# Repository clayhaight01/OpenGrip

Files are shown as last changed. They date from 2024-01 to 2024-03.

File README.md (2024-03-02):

# OpenGrip

### a simple, low-cost, robotics gripper

<div>
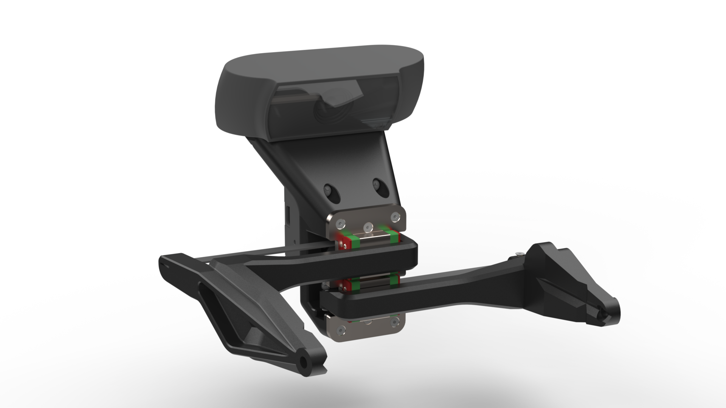
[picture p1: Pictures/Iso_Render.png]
Isometric Render of OpenGrip
  
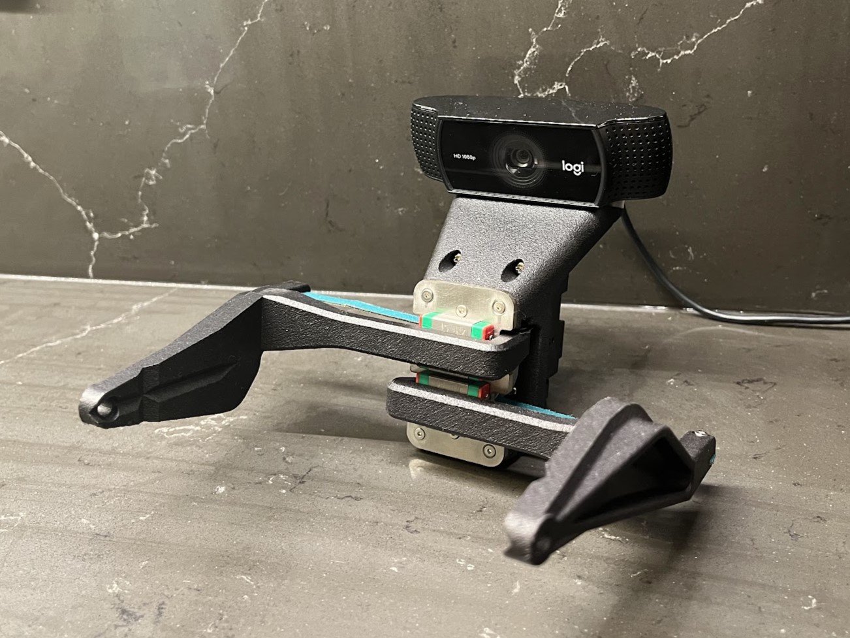
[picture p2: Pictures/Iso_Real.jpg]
Isometric View of the Actual OpenGrip
  
</div>

## overview

robotics grippers are often expensive, bulky, and challenging to integrate. OpenGrip offers a solution that is both affordable and user-friendly, without compromising on performance. 

### features

- **low cost**: by using only 5 custom parts and affordable hardware, OpenGrip significantly reduces costs, making it accessible for a wide range of users and applications

- **simple**: no belts, linkages, or gears - and constant force springs prevent collisions from damaging the gripper

- **high performance**: despite its cost-effectiveness, OpenGrip competes with the performance of grippers that are up to 50 times more expensive

- **adjustable compliance**: by using different winch materials (Nylon, Rubber, etc.) the compliance of the grasp can be adjusted

- **ease of use**: the Dynamixel servo motor makes OpenGrip extremely user-friendly. It can be controlled through ROS or any other Dynamixel-compatible control methods

## getting started

Assembly instructions can be found [here](https://docs.google.com/presentation/d/1iBIFQ8Uv3fJxjH3Wcjm2KIDGo_j1fCUzhZIH-ikzjmM/edit?usp=sharing)

BOM can be found [here](https://docs.google.com/spreadsheets/d/18ndGbQFCbwUeQNG1r3dqTShQs4zwCBGkiXpTbjC0DrM/edit?usp=sharing)

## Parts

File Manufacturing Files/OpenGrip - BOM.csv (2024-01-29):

OpenGrip | a simple, low cost, robotics gripper
Name | Configuration | Link | Price | Quantity | Total Price (USD) | Notes
Dynamixel Servo | XL430-W250 | https://www.robotis.us/dynamixel-xl430-w250-t/ | $49.90 | 1 | $49.90 | Use screws that come with it for pulley mounting
Constant Force Spring | 0.1x8x110 | https://www.aliexpress.com/item/1005002310168061.html | $6.52 | 2 | $13.04
Linear Rail & Carriage | 80 - MGN7C | https://www.aliexpress.com/item/1005004894759989.html | $13.41 | 2 | $26.82
Nylon Belt | 8in | https://www.mcmaster.com/6082K51-6082K202/ | $7.12 | 1 | $7.12 | If you want no compliance
Rubber Belt | 60mm | https://www.aliexpress.com/item/1005001961868127.html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 | $5.21 | 0 | $0.00 | If you want compliance
Silicone Padding | 300x30x1 | https://www.aliexpress.com/item/1005003757932880.html | $2.52 | 1 | $2.52
Heat Set Inserts | M2-M4 | https://www.aliexpress.com/item/1005005227477455.html | $18.93 | 1 | $18.93
M2 Flat Head | 5mm | https://www.mcmaster.com/92125A051/ | $10.80 | 1 | $10.80 | Multiple other sources
Screws | Cap | https://www.aliexpress.com/item/33033655207.html | $21.73 | 1 | $21.73
Screws | Flat | https://www.aliexpress.com/item/33033655207.html | $24.90 | 1 | $24.90
Webcam | C922X | https://www.amazon.com/Logitech-C922x-Pro-Stream-Webcam/dp/B01LXCDPPK | 79.99 | 0 | $0.00 | Optional
 |  |  |  | Total | $175.76
I used MJF for all the plastic parts from JLCPCB, but everything can be easily FDM printed.
File Name |  | Material | Manufacturing | Quantity | Notes
Gripper_Structure.STL |  | PA11/PLA | MJF/FDM | 1
Gripper_Jaw.STL |  | PA11/PLA | MJF/FDM | 2
CF_Spring_Idler.STL |  | PA11/PLA | MJF/FDM | 2
CF_Spring_Idler_Cap.STL |  | PA11/PLA | MJF/FDM | 2
Gripper_Carriage_Mount<...>.DXF or .STEP |  | Aluminum | Laser/Waterjet/CNC | 1 | I got from SendCutSend. If you want high force grasps, switch to stainless. If you want to lasercut/waterjet and countersink yourself, use the DXF. If you are CNCing use the STEP.
Gripper_Drive_Pulley.STL |  | PA11/PLA | MJF/FDM | 1
C922X_Pro_Clamp.STL |  | PA11/PLA | MJF/FDM | 0 | Optional, for webcam

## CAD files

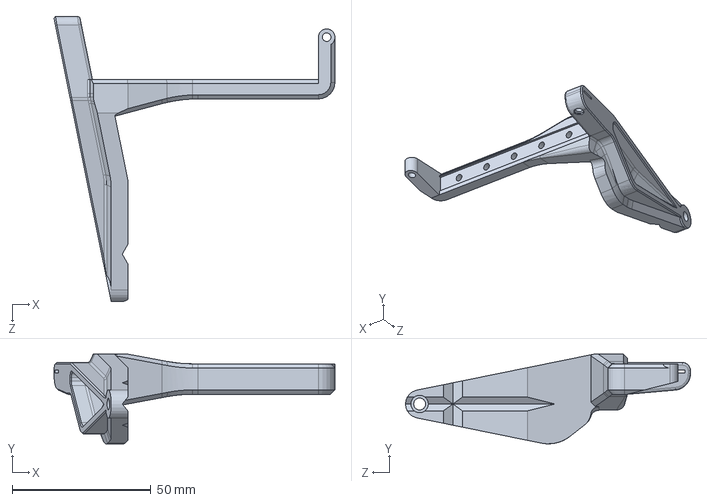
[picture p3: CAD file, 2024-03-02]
CAD/Gripper_Jaw.SLDPRT
101.4 x 32.4 x 102.8 mm

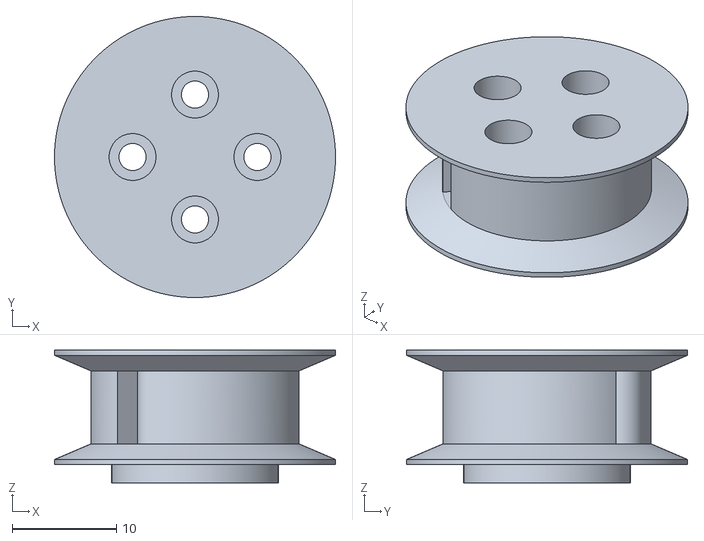
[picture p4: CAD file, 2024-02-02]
Manufacturing Files/Gripper_Drive_Pulley_XL330.STL
27.0 x 27.0 x 12.8

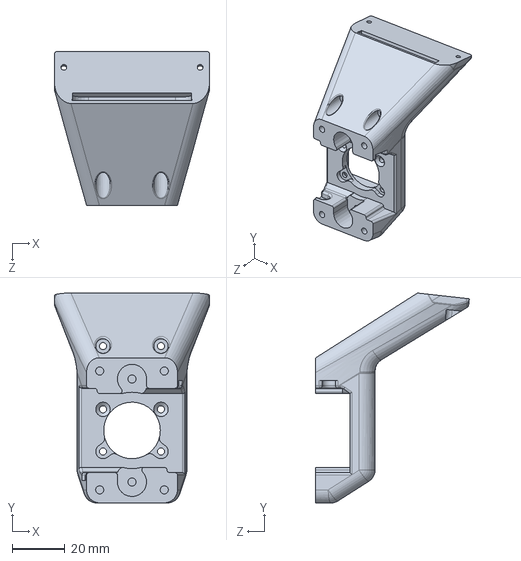
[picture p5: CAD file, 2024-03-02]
CAD/Gripper_Structure.SLDPRT
59.0 x 79.7 x 58.4 mm

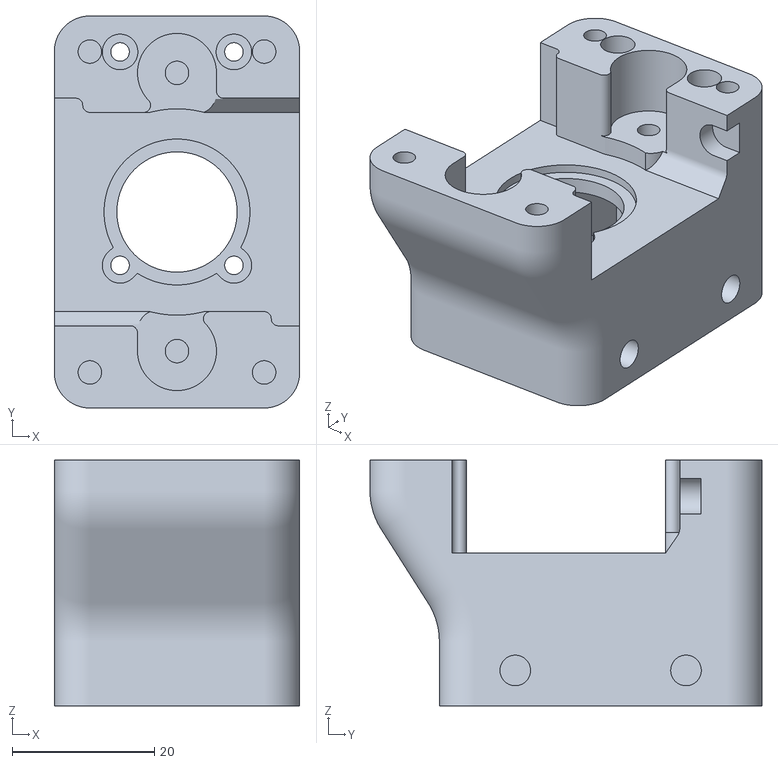
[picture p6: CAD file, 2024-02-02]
Manufacturing Files/Gripper_Structure_XL330.STL
34.5 x 55.1 x 34.6

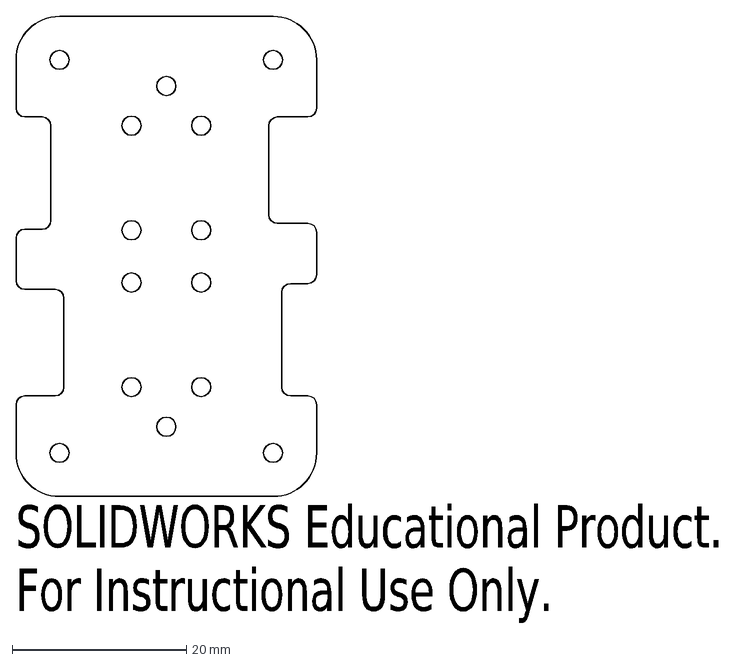
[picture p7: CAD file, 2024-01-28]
Manufacturing Files/Gripper_Carriage_Mount_2D_Method.DXF
SOLIDWORKS Educational Product.
For Instructional Use Only.

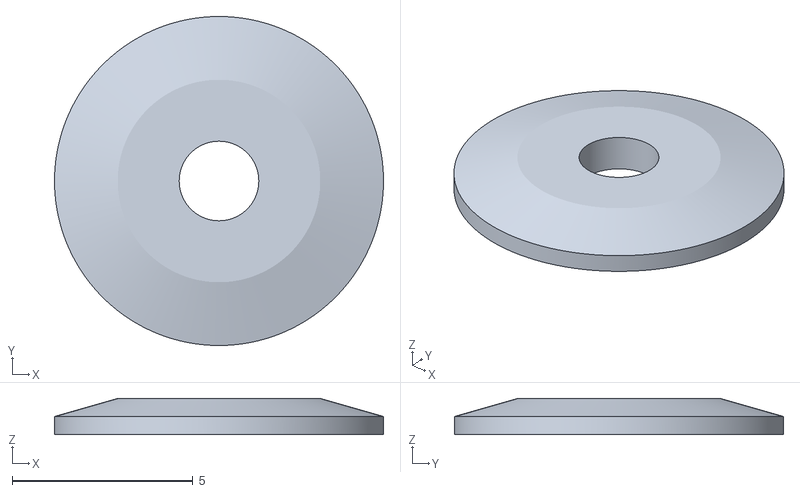
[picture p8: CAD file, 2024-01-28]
Manufacturing Files/CF_Spring_Idler_Cap.STL
9.10 x 9.10 x 1.00

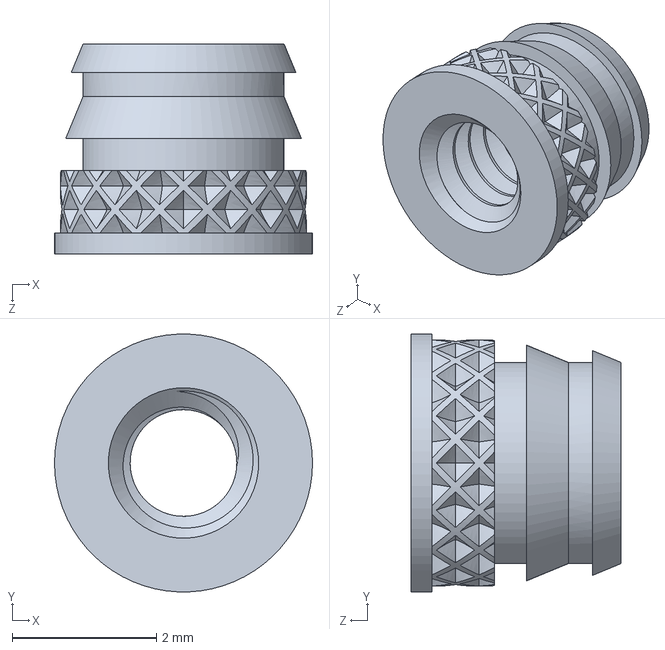
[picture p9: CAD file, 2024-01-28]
CAD/M2_Heatset.SLDPRT
3.58 x 3.58 x 2.92 mm

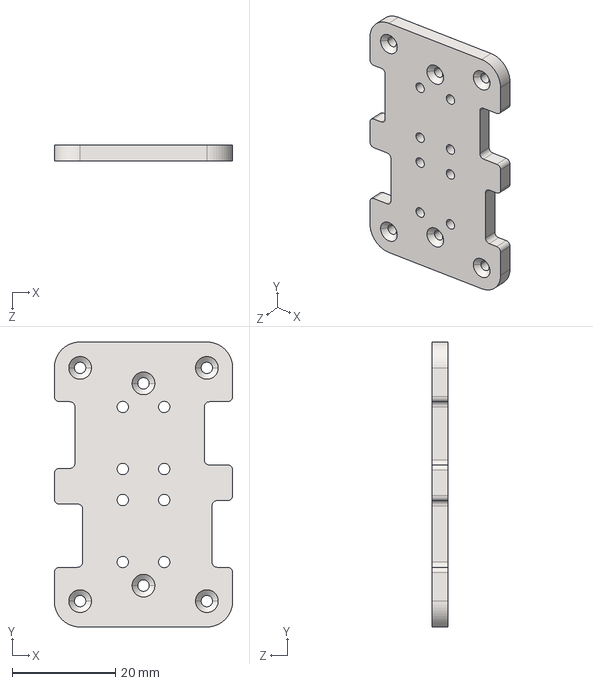
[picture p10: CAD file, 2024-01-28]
Manufacturing Files/Gripper_Carriage_Mount_CNC.STEP
34.5 x 55.1 x 3.17 mm

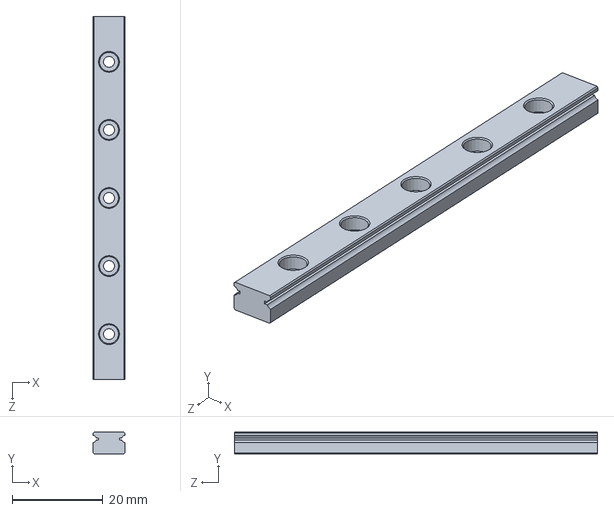
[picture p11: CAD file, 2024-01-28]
CAD/MGN7_Rail.SLDPRT
7.00 x 4.80 x 80.0 mm

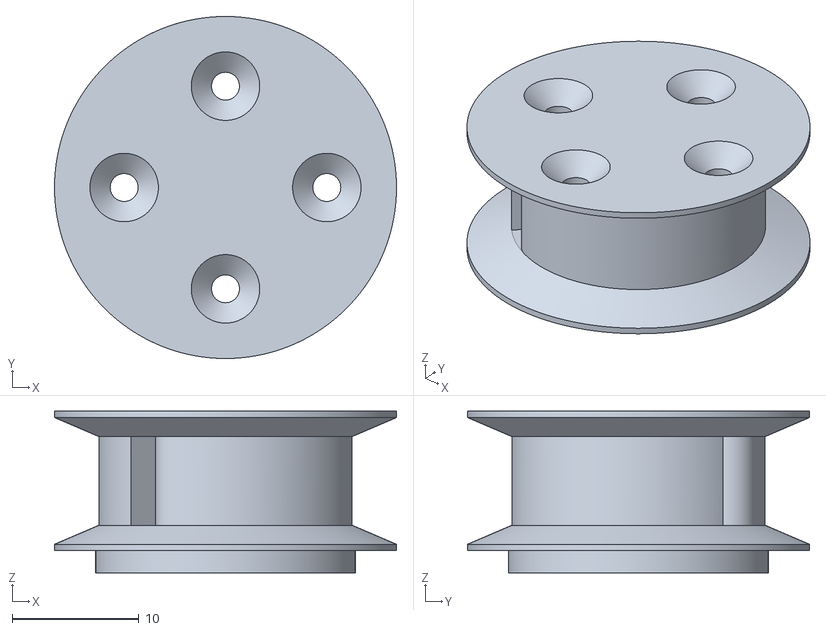
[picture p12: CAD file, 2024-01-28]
Manufacturing Files/Gripper_Drive_Pulley.STL
27.0 x 27.0 x 12.8

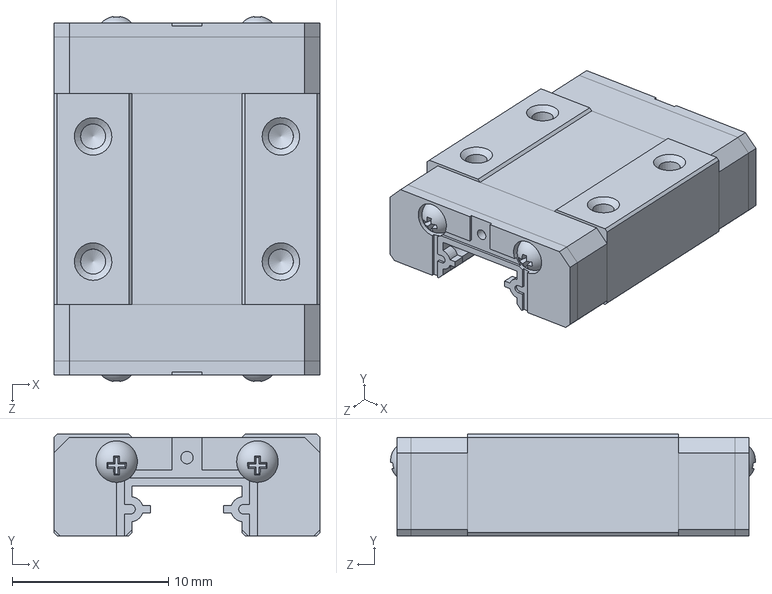
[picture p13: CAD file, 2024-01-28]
CAD/MGN7C_Carriage.SLDPRT
17.0 x 6.50 x 23.3 mm

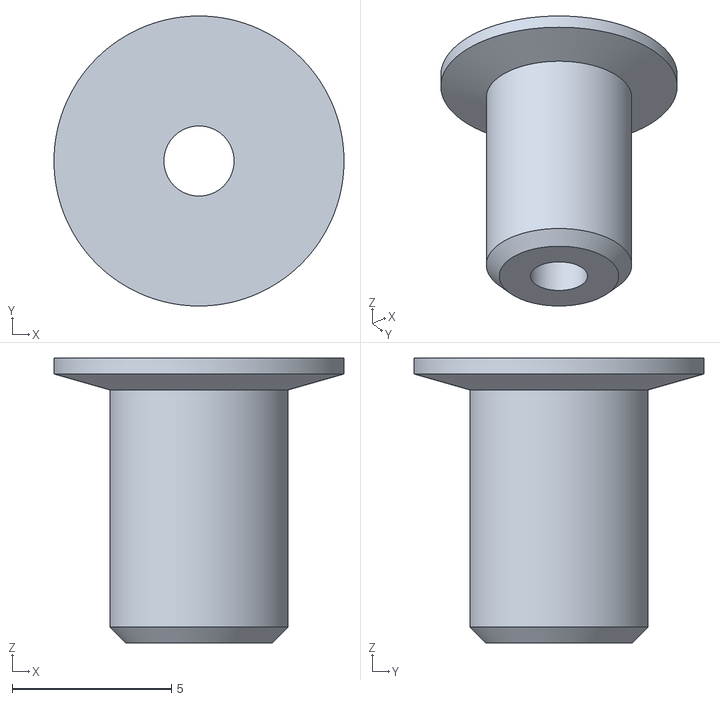
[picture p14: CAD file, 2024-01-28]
Manufacturing Files/CF_Spring_Idler.STL
9.10 x 9.10 x 8.94

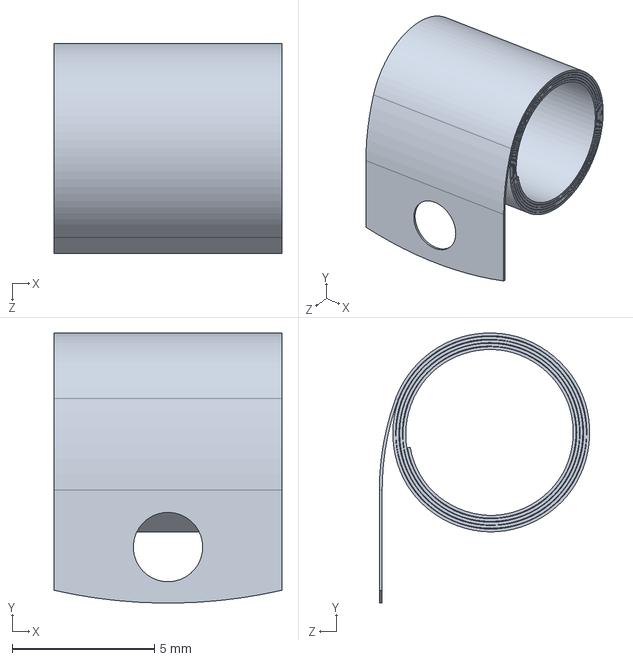
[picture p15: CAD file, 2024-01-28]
CAD/0.1x8x110_CF.SLDPRT
8.00 x 9.49 x 7.39 mm

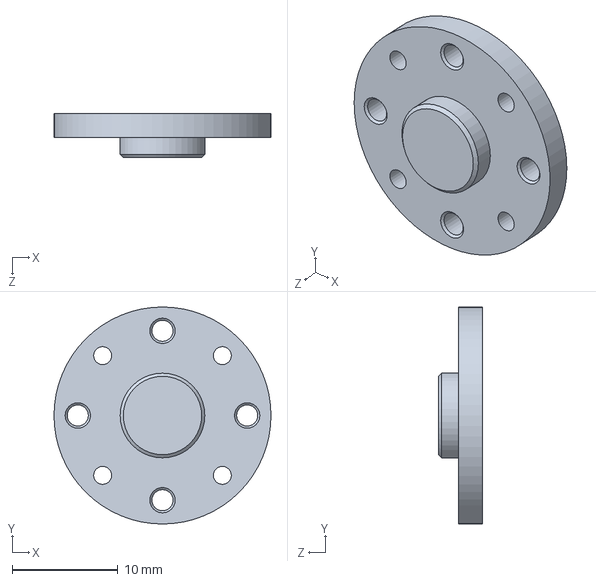
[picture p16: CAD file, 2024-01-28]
CAD/430_Horn.SLDPRT
20.5 x 20.5 x 4.15 mm

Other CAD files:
CAD/Gripper_Structure_XL330.SLDPRT
CAD/Gripper_Drive_Pulley_XL330.SLDPRT
CAD/Drive Belt.SLDPRT
CAD/Gripper_Carriage_Mount.SLDPRT
CAD/91292A831_18-8 Stainless Steel Socket Head Screw.SLDPRT
CAD/92000A108_Passivated 18-8 Stainless Steel Pan Head Phillips Screws.SLDPRT
CAD/92010A775_Passivated 18-8 Stainless Steel Phillips Flat Head Screw.SLDPRT
CAD/92125A051_18-8 Stainless Steel Hex Drive Flat Head Screw.SLDPRT
CAD/92125A054_18-8 Stainless Steel Hex Drive Flat Head Screw.SLDPRT
CAD/92125A059_18-8 Stainless Steel Hex Drive Flat Head Screw.SLDPRT
CAD/C922X_Pro.SLDPRT
CAD/CF_Spring_Idler.SLDPRT
CAD/CF_Spring_Idler_Cap.SLDPRT
CAD/Gripper_Drive_Pulley.SLDPRT
CAD/Servo_Geo.SLDPRT
CAD/XL-430.SLDPRT

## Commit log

2024-01-28 Added renders, cleaned up structure
    [0.1x8x110_CF.SLDPRT, 430_Horn.SLDPRT, 91292A831_18-8 Stainless Steel Socket Head Screw.SLDPRT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]
2024-02-02 Added XL330/no camera option
    [Gripper_Drive_Pulley_XL330.SLDPRT, Gripper_Drive_Pulley_XL330.STL, Gripper_Structure_XL330.SLDPRT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]
2024-02-28 Assembly instructions added
2024-03-02 Heat set hole size adjustment
    [Gripper_Structure.SLDPRT]
2024-03-02 Made belt width 0.25mm bigger
    [Gripper_Jaw.SLDPRT]
